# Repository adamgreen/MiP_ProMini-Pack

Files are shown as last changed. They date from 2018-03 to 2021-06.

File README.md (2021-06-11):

# MiP ProMini Pack - 16MHz/5V
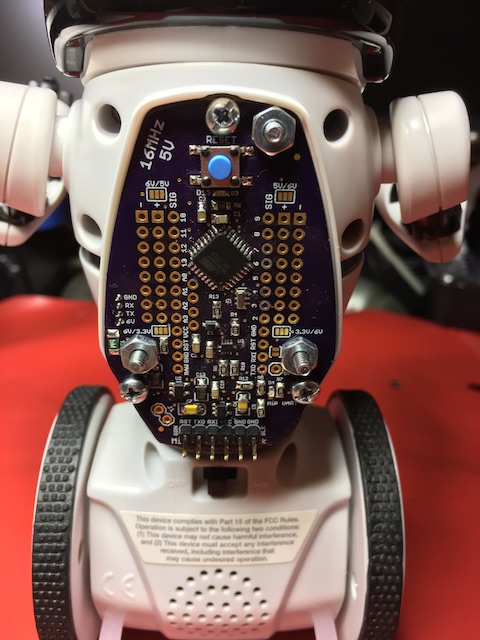
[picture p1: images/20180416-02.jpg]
MiP with ProMini Pack on its back


# Archived - June 10th, 2021
This project is no longer under active development. Both @Tiogaplanet and I have moved onto other projects.

# Attribution
This project is based on the now retired [Sparkfun MiP ProMini-Pack](https://www.sparkfun.com/products/retired/13058).<br>
The original Eagle files can be found on [GitHub](https://github.com/sparkfun/MiP_ProMini-Pack). They were created by
Sparkfun employee [Casey Kuhns](https://github.com/caseykuhns).

# Project Goals
* Produce a functional version of the MiP ProMini-Pack to correct the [MiP communication issue](https://github.com/WowWeeLabs/MiP-BLE-Protocol/issues/18) in the Sparkfun original.
* Run the ATMEGA328 at 16MHz instead of 8MHz. This allows the AVR to properly receive 115200 bps serial output from the
  MiP.
* Increase Vcc from 3.3V to 5V so that the ATMEGA328 can reliably run at 16MHz.
* Modify board layout to make it easier to hand solder the SMD parts.
  * Use larger 0805 passives instead of 0603.
  * Extend the pads on some of the SMD packages to allow for easier transfer of heat from the soldering iron.
* Port my [MiP C API](https://github.com/adamgreen/MiP-Capi) project to Arduino and refactor it to make it more closely resemble other Arduino libraries.
  * This library can be found within the [Arduino/MiP_ProMini_Pack_Library](Arduino/MiP_ProMini_Pack_Library#readme) folder of this GitHub repository.

# Links
* [MiP ProMini-Pack Arduino Library](Arduino/MiP_ProMini_Pack_Library#readme): The Arduino library for this MiP ProMini-Pack.<br>
* [WowWee's Official MiP Protocol Specification](https://github.com/WowWeeLabs/MiP-BLE-Protocol): Describes the serial protocol used by the Arduino library to communicate with the MiP.<br>
* [Sparkfun's MiP ProMini-Pack Installation Tutorial](https://learn.sparkfun.com/tutorials/hacking-the-mip---promini-pack): This retired Sparkfun tutorial is still the best place to learn about opening up your MiP and installing this MiP ProMini Pack.<br>
* [Tiogaplanet's MiP ProtoPack](https://github.com/Tiogaplanet/MiP_ProtoPack): A prototyping plug-in board to expand the MiP ProMini-Pack.<br>

# Bill of Materials
Description | Quantity | Part Number(s)
------------|----------|---------------
[TS3USB221A USB SWITCH DUAL - 10QFN](https://www.digikey.com/products/en?keywords=296-24019-1-ND) | 1 | U3
[ATMEGA328P - 32TQFP](https://www.digikey.com/products/en?keywords=ATMEGA328P-AURCT-ND) | 1 | U1
[16MHz Ceramic Resonator - 15pF ±0.2% SMD](https://www.digikey.com/products/en?keywords=490-1198-1-ND) | 1 | Q1
[MIC5205 Linear Regulator - 5.0V 150mA SOT23-5](https://www.digikey.com/products/en?keywords=576-1261-1-ND) | 1 | U2
[MIC5205 Linear Regulator - 3.3V 150mA SOT23-5](https://www.digikey.com/products/en?keywords=576-1259-1-ND) | 1 | U4
[10kΩ Resistor - 0805](https://www.adafruit.com/product/441) | 3 | R2, R4, R5
[1kΩ Resistor - 0805](https://www.adafruit.com/product/441) | 6 | R7, R8, R9, R10, R12, R13
[330Ω Resistor - 0805](https://www.adafruit.com/product/441) | 1 | R6
[0.1uF Capacitor - 0805](https://www.adafruit.com/product/441) | 6 | C1, C2, C3, C4, C5, C10
[10uF Capacitor - 1206](https://www.digikey.com/products/en?keywords=478-8235-1-ND) | 4 | C6, C7, C13, C19
[Diode Schottky 10V 570mA SOD323](https://www.digikey.com/products/en?keywords=ZLLS410CT-ND) | 1 | D1
[Green LED - 0603](https://www.digikey.com/products/en?keywords=160-1446-1-ND) | 2 | D3, D4
[PTC Resettable Fuse - 1206](https://www.digikey.com/products/en?keywords=507-1802-1-ND) | 1 | F1
[SPST Tactile SMD Switch - Normally Open](https://www.digikey.com/products/en?keywords=CKN9112CT-ND) | 1 | S1
[JST 4-position Connector - 1.5mm Through-Hole](https://www.digikey.com/products/en?keywords=455-1659-ND) | 1 | JP11
[Male Header for FTDI 1x6 - 0.1" Through-Hole](https://www.digikey.com/products/en?keywords=HDR100IMP40M-G-V-TH-ND) | 1 | JP1
[JST 4-wire Cable](https://www.digikey.com/product-detail/en/jst-sales-america-inc/A04ZR04ZR28H152A/455-3026-ND/6009402) | 1 |
[Screw - Phillips Head (1/2", 4-40)](https://www.sparkfun.com/products/10452) | 3 |
[Nut - (4-40)](https://www.sparkfun.com/products/10454) | 3 |
[Screw - Phillip Head (M3-0.5 x 12mm)](https://www.sparkfun.com/products/13227) | 3 |

# Schematic
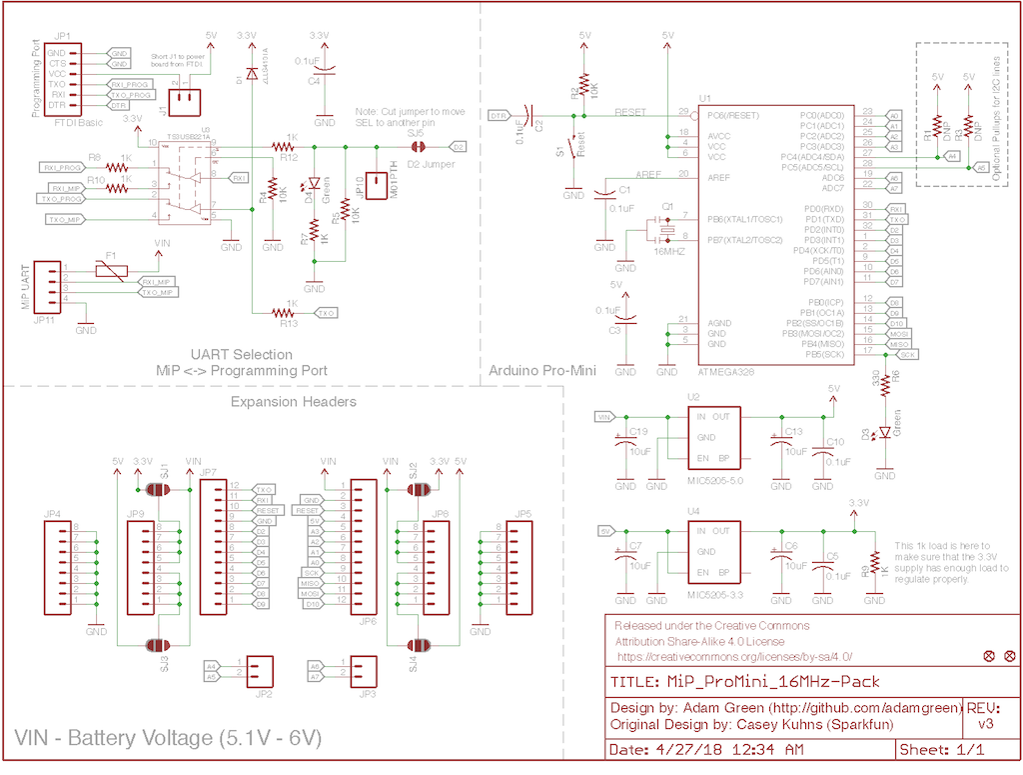
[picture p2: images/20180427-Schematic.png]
Schematic


# OSHPark Renderings of PCB
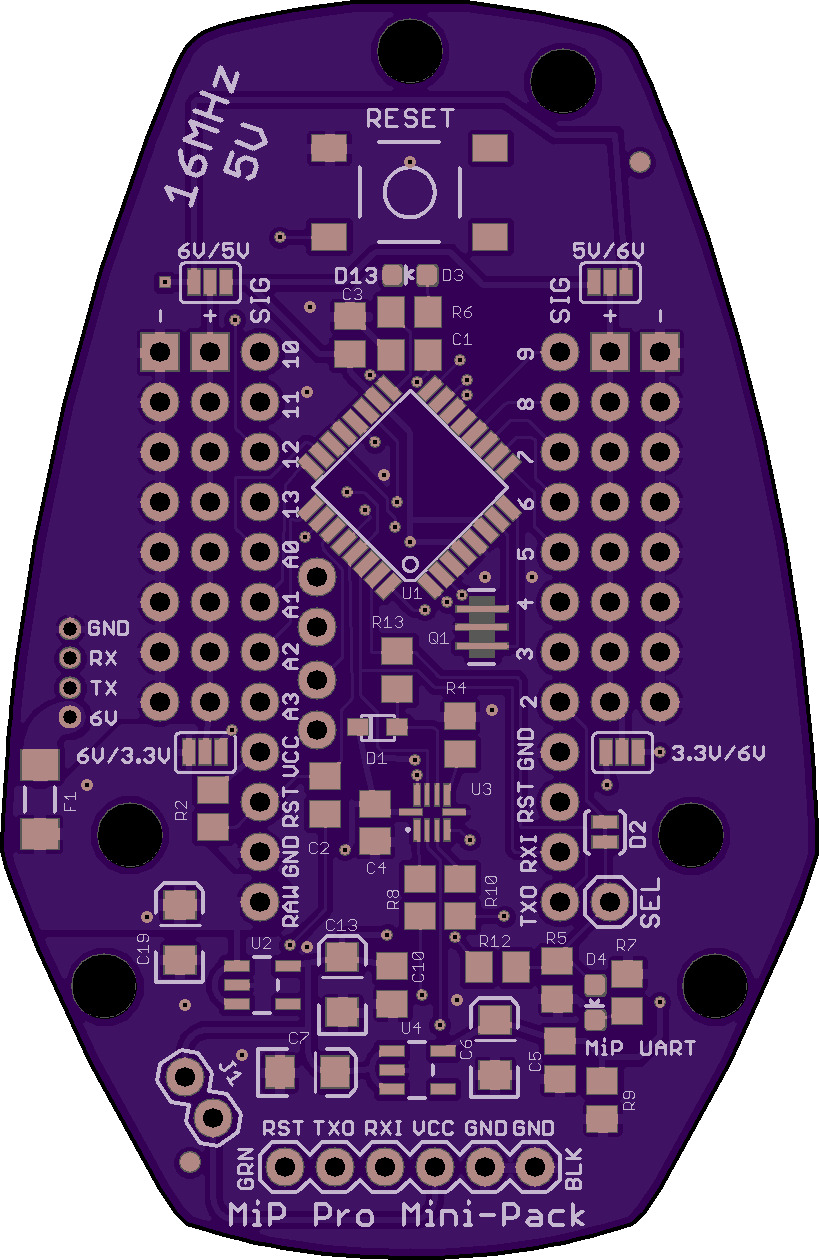
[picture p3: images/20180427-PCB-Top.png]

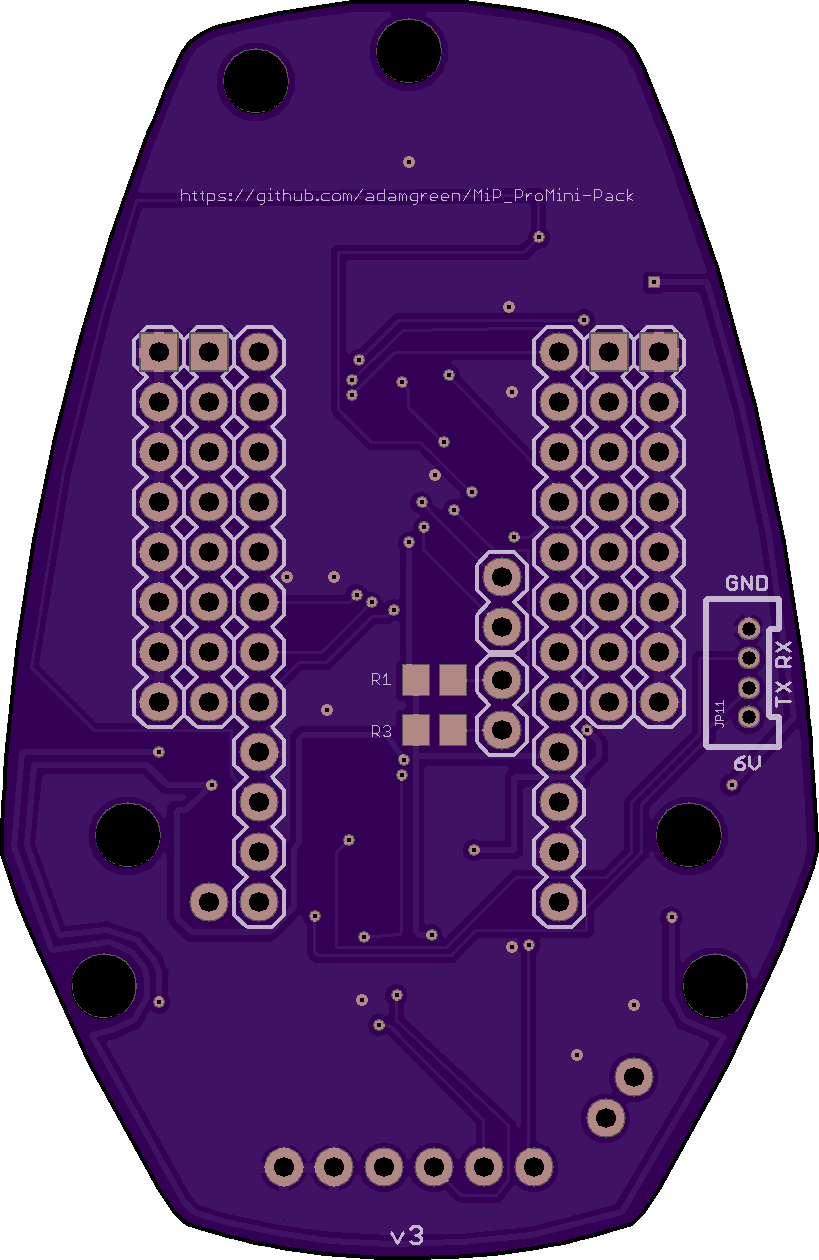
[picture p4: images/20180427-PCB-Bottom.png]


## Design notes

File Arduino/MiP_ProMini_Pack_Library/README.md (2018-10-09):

# MiP ProMini Pack Arduino Library
MiP Photo<br>
The [WowWee MiP](https://wowwee.com/mip) is a hacker friendly self-balancing robot. WowWee not only publish the [MiP Protocol Specification on GitHub](https://github.com/WowWeeLabs/MiP-BLE-Protocol), they also provide a [4-pin hacker port](https://cdn.sparkfun.com/assets/learn_tutorials/2/8/5/HackingPortAnnotated.png), complete with JST connector, right on the mainboard. This connector makes it easy to connect the Arduino compatible [MiP ProMini Pack](https://github.com/adamgreen/MiP_ProMini-Pack) and take control of your MiP. Once connected, you can start:
* Commanding the speed and direction of motion for the gravity defying MiP.
* Commanding the individual control (on, off, blink) of the 4 LED eye segments on the head.
* Taking full control of the RGB LED in the MiP's chest.
* Commanding the playback of sound lists using the >100 built-in sounds.
* Using the head mounted IR sensors to read 'radar' distance measurements or detected user hand gestures.
* Detecting user claps with the built-in microphone.
* Detecting the MiP's current pose via its inertial sensors, the same sensors that make its balancing magic possible.
* And More!

The MiP ProMini Pack was [originally designed by Sparkfun](https://www.sparkfun.com/products/retired/13058) but has since been retired. [This retired Sparkfun tutorial](https://learn.sparkfun.com/tutorials/hacking-the-mip---promini-pack) is still the best place to learn about opening up your MiP and installing the MiP ProMini Pack. Once installed, this is what your MiP will look like:<br>
MiP with ProMini Pack on its back<br>
Once you have it mounted, attach your [FTDI cable](https://www.sparkfun.com/products/9718), [install the MiP ProMini Pack library in the Arduino IDE](https://learn.sparkfun.com/tutorials/installing-an-arduino-library), start hacking and have fun!

## Limitations
One of the cool features that Sparkfun built into the original MiP ProMini Pack is the ability to use the hardware Serial port for communicating with both the MiP and the Arduino IDE's serial monitor. It accomplishes this great feat by using a switch that can direct the Serial traffic to the appropriate target based on the setting of pin 2. Once you call begin() on the MiP object, the Serial traffic will be directed to the MiP except when your code issues print commands such as ```Serial.println("Hello World");```. The library will detect such print calls and automatically direct the resulting Serial traffic to the Arduino IDE and then switch it back to the MiP once the data has been received by the Arduino IDE.

What limitations does this put on your usage of ```Serial.println()``` and ```Serial.print()``` calls?
* Don't use other libraries which send information to the Arduino IDE. Their data will end up being sent to the MiP instead. Only code which ```#include <mip.h>``` will automatically have their print output redirected to the Arduino IDE.
* There are some functions in the library that rely on receiving updates/events that the MiP sends to your Arduino while you are running your awesome code. These include:
  * Radar measurement updates
  * Hand gesture events
  * Battery level updates
  * MiP pose updates (standing upright, laying face down, etc)
  * Clap events
  * Weight updates
  * Shake events
  * Infrared events (detecting other MiPs and receiving their IR codes)
* If you are sending a lot of data to the Arduino IDE in between MiP function calls, you might cause these updates/events to be lost.
* There is a LED labelled **MiP UART** towards the lower right corner of the MiP ProMini Pack. This will be lit when Serial is switched to exchange data with the MiP.
* If you see that it is off most of the time, then you are likely to miss these updates/events.
* If you find your code isn't receiving expected updates/events then double check that you aren't sending too much data to the Arduino IDE.
* It is probably best to not attempt receiving data sent from the Arduino IDE. Calling functions like ```Serial.read()``` from your code is likely to read MiP updates and not Arduino IDE data from the Serial receive buffer.

The original MiP robots communicated over the UART at 115200 baud but the newer ones now communicate at 9600 baud. This library will first start to connect with the MiP at 115200 baud in the MiP::begin() call. If this fails after 5 retries, it will switch to 9600 baud and try again (up to 5 retries). This means that the library should work with both new and old MiP robots but may take a second or so longer to connect to the newer MiP robots when it tries 115200 baud initially.

## Examples
* [ChestLED](https://github.com/adamgreen/MiP_ProMini-Pack/blob/master/Arduino/MiP_ProMini_Pack_Library/examples/ChestLED/ChestLED.ino): Take control of the RGB LED in the chest of the MiP.
* [Clap](https://github.com/adamgreen/MiP_ProMini-Pack/blob/master/Arduino/MiP_ProMini_Pack_Library/examples/Clap/Clap.ino): Send descriptive messages to the Arduino IDE about each clap event deteced by the MiP robot.
* [ContinuousDrive](https://github.com/adamgreen/MiP_ProMini-Pack/blob/master/Arduino/MiP_ProMini_Pack_Library/examples/ContinuousDrive/ContinuousDrive.ino): You want to control the motion of the MiP in real time? This is the example for you.
* [DisconnectApp](https://github.com/adamgreen/MiP_ProMini-Pack/blob/master/Arduino/MiP_ProMini_Pack_Library/examples/DisconnectApp/DisconnectApp.ino): Disconnect all apps, including this sketch and any app that may be connected to Bluetooth.
* [DistanceDrive](https://github.com/adamgreen/MiP_ProMini-Pack/blob/master/Arduino/MiP_ProMini_Pack_Library/examples/DistanceDrive/DistanceDrive.ino): Tell the MiP robot exactly how far to travel and forget about it.
* [DriveForwardBackward](https://github.com/adamgreen/MiP_ProMini-Pack/blob/master/Arduino/MiP_ProMini_Pack_Library/examples/DriveForwardBackward/DriveForwardBackward.ino): Tell the MiP robot how long to drive forward/backward and forget about it.
* [EnableGameMode](https://github.com/adamgreen/MiP_ProMini-Pack/blob/master/Arduino/MiP_ProMini_Pack_Library/examples/EnableGameMode/EnableGameMode.ino): Cycle through each of the game modes available.
* [EnableMiPDetectionMode](https://github.com/adamgreen/MiP_ProMini-Pack/blob/master/Arduino/MiP_ProMini_Pack_Library/examples/EnableMiPDetectionMode/EnableMiPDetectionMode.ino): Allow your MiP to be discovered by others.
* [FallDown](https://github.com/adamgreen/MiP_ProMini-Pack/blob/master/Arduino/MiP_ProMini_Pack_Library/examples/FallDown/FallDown.ino): Tired of standing around? Command MiP to fall flat on his face.
* [Gesture](https://github.com/adamgreen/MiP_ProMini-Pack/blob/master/Arduino/MiP_ProMini_Pack_Library/examples/Gesture/Gesture.ino): Use your hand to make gesture to your MiP robot. Send descriptive messages to the Arduio IDE about each gesture event detected.
* [GestureRadarMode](https://github.com/adamgreen/MiP_ProMini-Pack/blob/master/Arduino/MiP_ProMini_Pack_Library/examples/GestureRadarMode/GestureRadarMode.ino): Want to learn more about how to enable/disable IR based gesture and radar measurements? Check out this example.
* [GetUp](https://github.com/adamgreen/MiP_ProMini-Pack/blob/master/Arduino/MiP_ProMini_Pack_Library/examples/GetUp/GetUp.ino): If your MiP robot falls down, learn how to have him try getting back up on his ~~feet~~wheels.
* [HeadLEDs](https://github.com/adamgreen/MiP_ProMini-Pack/blob/master/Arduino/MiP_ProMini_Pack_Library/examples/HeadLEDs/HeadLEDs.ino): Take control of the 4 individual eye LEDs on the MiP robot's head.
* [Odometer](https://github.com/adamgreen/MiP_ProMini-Pack/blob/master/Arduino/MiP_ProMini_Pack_Library/examples/Odometer/Odometer.ino): How far has your MiP robot been traveling around your personal robot laboratory? This example shows you how to find out and reset its measurement.
* [PlaySound](https://github.com/adamgreen/MiP_ProMini-Pack/blob/master/Arduino/MiP_ProMini_Pack_Library/examples/PlaySound/PlaySound.ino): Learn how to get the MiP robot vocalizing under your control!
* [Radar](https://github.com/adamgreen/MiP_ProMini-Pack/blob/master/Arduino/MiP_ProMini_Pack_Library/examples/Radar/Radar.ino): Is there anything in front of your MiP robot? This example sends descriptive text to the Arduino IDE when it detects changes in the obstacles around it.
* [RawSendReceive](https://github.com/adamgreen/MiP_ProMini-Pack/blob/master/Arduino/MiP_ProMini_Pack_Library/examples/RawSendReceive/RawSendReceive.ino): You found a command in WowWee's Protocol Specification that isn't supported by this library? This example shows you how to experiment with these new commands.
* [ReadWriteEeprom](https://github.com/adamgreen/MiP_ProMini-Pack/blob/master/Arduino/MiP_ProMini_Pack_Library/examples/ReadWriteEeprom/ReadWriteEeprom.ino): Read and write your own data to MiP's EEPROM. This is useful for storing data across power cycles. See also [ZeroEeprom](https://github.com/adamgreen/MiP_ProMini-Pack/blob/master/Arduino/MiP_ProMini_Pack_Library/examples/ZeroEeprom/ZeroEeprom.ino).
* [ReadIRDongleCode](https://github.com/adamgreen/MiP_ProMini-Pack/blob/master/Arduino/MiP_ProMini_Pack_Library/examples/ReadIRDongleCode/ReadIRDongleCode.ino): Reads IR signals sent from another MiP. See also [SendIRDongleCode](https://github.com/adamgreen/MiP_ProMini-Pack/blob/master/Arduino/MiP_ProMini_Pack_Library/examples/SendIRDongleCode/SendIRDongleCode.ino).
* [SendIRDongleCode](https://github.com/adamgreen/MiP_ProMini-Pack/blob/master/Arduino/MiP_ProMini_Pack_Library/examples/SendIRDongleCode/SendIRDongleCode.ino): Sends IR signals to another MiP. See also [ReadIRDongleCode](https://github.com/adamgreen/MiP_ProMini-Pack/blob/master/Arduino/MiP_ProMini_Pack_Library/examples/ReadIRDongleCode/ReadIRDongleCode.ino).
* [SRSdemo](https://github.com/adamgreen/MiP_ProMini-Pack/blob/master/Arduino/MiP_ProMini_Pack_Library/examples/SRSdemo/SRSdemo.ino): The MiP robot made an appearance at the [Seattle Robotics Society](http://www.seattlerobotics.org) meeting on April 21st, 2018. This is what he was running!
* [Shake](https://github.com/adamgreen/MiP_ProMini-Pack/blob/master/Arduino/MiP_ProMini_Pack_Library/examples/Shake/Shake.ino): Is someone shaking your poor little MiP robot? This example shows you how to detect such rudeness and report it to the Arduino IDE.
* [SoftwareHardwareVersion](https://github.com/adamgreen/MiP_ProMini-Pack/blob/master/Arduino/MiP_ProMini_Pack_Library/examples/SoftwareHardwareVersion/SoftwareHardwareVersion.ino): This example shows you how to peek under the covers and see what hardware / software is running inside your MiP robot.
* [Status](https://github.com/adamgreen/MiP_ProMini-Pack/blob/master/Arduino/MiP_ProMini_Pack_Library/examples/Status/Status.ino): Detect changes in the MiP robot's battery level or pose and report them to the Arduino IDE.
* [Stop](https://github.com/adamgreen/MiP_ProMini-Pack/blob/master/Arduino/MiP_ProMini_Pack_Library/examples/Stop/Stop.ino): Danger! Danger! MiP Robot! Stop your MiP robot in its tracks before it gets itself into more trouble.
* [TurnLeftRight](https://github.com/adamgreen/MiP_ProMini-Pack/blob/master/Arduino/MiP_ProMini_Pack_Library/examples/TurnLeftRight/TurnLeftRight.ino): Tell the MiP robot exactly how many degrees to turn and forget about it.
* [Volume](https://github.com/adamgreen/MiP_ProMini-Pack/blob/master/Arduino/MiP_ProMini_Pack_Library/examples/Volume/Volume.ino): Your MiP robot is too loud? Turn down the volume with this example.
* [Weight](https://github.com/adamgreen/MiP_ProMini-Pack/blob/master/Arduino/MiP_ProMini_Pack_Library/examples/Weight/Weight.ino): Detect weight changes in what the MiP is carrying and report them to the Arduino IDE.
* [ZeroEeprom](https://github.com/adamgreen/MiP_ProMini-Pack/blob/master/Arduino/MiP_ProMini_Pack_Library/examples/ZeroEeprom/ZeroEeprom.ino): Write zeroes to each available byte in EEPROM. See also [ReadWriteEeprom](https://github.com/adamgreen/MiP_ProMini-Pack/blob/master/Arduino/MiP_ProMini_Pack_Library/examples/ReadWriteEeprom/ReadWriteEeprom.ino).

## Functions
Group | Function
----- | --------
Initialization  | [MiP()](#mip)
<br>            | [begin()](#begin)
<br>            | [end()](#end)
<br>            | [sleep()](#sleep)
<br>            | [isInitialized()](#isinitialized)
Radar           | [enableRadarMode()](#enableradarmode)
<br>            | [disableRadarMode()](#disableradarmode)
<br>            | [isRadarModeEnabled()](#isradarmodeenabled)
<br>            | [areGestureAndRadarModesDisabled()](#aregestureandradarmodesdisabled)
<br>            | [readRadar()](#readradar)
Gesture         | [enableGestureMode()](#enablegesturemode)
<br>            | [disableGestureMode()](#disablegesturemode)
<br>            | [isGestureModeEnabled()](#isgesturemodeenabled)
<br>            | [areGestureAndRadarModesDisabled()](#aregestureandradarmodesdisabled)
<br>            | [availableGestureEvents()](#availablegestureevents)
<br>            | [readGestureEvent()](#readgestureevent)
Chest LED       | [writeChestLED()](#writechestled)
<br>            | [readChestLED()](#readchestled)
<br>            | [unverifiedWriteChestLED()](#unverifiedwritechestled)
Head LEDs       | [writeHeadLEDs()](#writeheadleds)
<br>            | [readHeadLEDs()](#readheadleds)
<br>            | [unverifiedWriteHeadLEDs()](#unverifiedwriteheadleds)
Motion          | [continuousDrive()](#continuousdrive)
<br>            | [distanceDrive()](#distancedrive)
<br>            | [turnLeft()](#turnleft)
<br>            | [turnRight()](#turnright)
<br>            | [driveForward()](#driveforward)
<br>            | [driveBackward()](#drivebackward)
<br>            | [stop()](#stop)
<br>            | [fallForward()](#fallforward)
<br>            | [fallBackward()](#fallbackward)
<br>            | [getUp()](#getup)
Sound           | [playSound()](#playsound)
<br>            | [beginSoundList()](#beginsoundlist)
<br>            | [addEntryToSoundList()](#addentrytosoundlist)
<br>            | [playSoundList()](#playsoundlist)
<br>            | [writeVolume()](#writevolume)
<br>            | [readVolume()](#readvolume)
Odometer        | [readDistanceTravelled()](#readdistancetravelled)
<br>            | [resetDistanceTravelled()](#resetdistancetravelled)
Battery Level   | [readBatteryVoltage()](#readbatteryvoltage)
Position        | [readPosition()](#readposition)
<br>            | [isOnBack()](#isonback)
<br>            | [isFaceDown()](#isfacedown)
<br>            | [isUpright()](#isupright)
<br>            | [isPickedUp()](#ispickedup)
<br>            | [isHandStanding()](#ishandstanding)
<br>            | [isFaceDownOnTray()](#isfacedownontray)
<br>            | [isOnBackWithKickstand()](#isonbackwithkickstand)
Weight          | [readWeight()](#readweight)
Clap            | [enableClapEvents()](#enableclapevents)
<br>            | [disableClapEvents()](#disableclapevents)
<br>            | [areClapEventsEnabled()](#areclapeventsenabled)
<br>            | [writeClapDelay()](#writeclapdelay)
<br>            | [readClapDelay()](#readclapdelay)
<br>            | [availableClapEvents()](#availableclapevents)
<br>            | [readClapEvent()](#readclapevent)
Shake           | [hasBeenShaken()](#hasbeenshaken)
Version Info    | [readSoftwareVersion()](#readsoftwareversion)
<br>            | [readHardwareInfo()](#readhardwareinfo)
Game Modes      | [enableAppMode()](#enableappmode)
<br>            | [enableCageMode()](#enablecagemode)
<br>            | [enableDanceMode()](#enabledancemode)
<br>            | [enableStackMode()](#enablestackmode)
<br>            | [enableTrickMode()](#enabletrickmode)
<br>            | [enableRoamMode()](#enableroammode)
<br>            | [isAppModeEnabled()](#isappmodeenabled)
<br>            | [isCageModeEnabled()](#iscagemodeenabled)
<br>            | [isDanceModeEnabled()](#isdancemodeenabled)
<br>            | [isStackModeEnabled()](#isstackmodeenabled)
<br>            | [isTrickModeEnabled()](#istrickmodeenabled)
<br>            | [isRoamModeEnabled()](#isroammodeenabled)
EEPROM          | [setUserData()](#setUserData)
<br>            | [getUserData()](#getUserData)
Infrared        | [enableMiPDetectionMode()](#enablemipdetectionmode)
<br>            | [disableMiPDetectionMode()](#disablemipdetectionmode)
<br>            | [isMiPDetectionModeEnabled()](#ismipdetectionmodeenabled)
<br>            | [readDetectedMiP()](#readdetectedmip)
<br>            | [availableDetectedMiPEvents()](#availabledetectedmipevents)
<br>            | [sendIRDongleCode()](#sendirdonglecode)
<br>            | [readIRDongleCode()](#readirdonglecode)
<br>            | [availableIRCodeEvents()](#availableircodeevents)

---
### MiP()
```MiP(int8_t serialSelectPin = MIP_UART_SELECT_PIN)```
#### Description
This MiP constructor is used to create an instance of a MiP object, whose name you need to provide as in the example below. Only one MiP object should be created in your sketch.

You still need to call [begin()](#begin) to initialize communication with the MiP before calling any other MiP functions.

#### Parameters
* **serialSelectPin** is the pin used to switch the Serial output between the MiP and Arduino IDE. It defaults to MIP_UART_SELECT_PIN, pin 2. The MiP ProMini Pack hardware is designed to use this pin as well. Switching serialSelectPin to another pin would therefore require that you make hardware changes to the MiP ProMini Pack as well.

#### Returns
Nothing

#### Example
```c++
// Include the MiP library so that you can use its functions.
#include <mip.h>

// Setup new MiP object.
MiP     mip;
```

---
### begin()
```bool MiP::begin()```
#### Description
Initializes the MiP robot to be controlled by the Arduino instead of Bluetooth Low Energy. The LED on the chest of the MiP robot will switch from blue to green once this switch has been made. The MiP robot requires a power reset to switch out of serial mode and accept Bluetooth Low Energy connections again.

Calling another MiP function before begin() has successfully been called will typically generate an error message and your program will be halted so that you can diagnose and correct the problem.

[isInitialized()](#isinitialized) can be called to determine if begin() has been successfully called or not.

#### Parameters
None

#### Returns
* **true** if the MiP robot was successfully initialized.
* **false** if begin() failed to properly initialize the MiP robot.

#### Example
```c++
// Include the MiP library so that you can use its functions.
#include <mip.h>

// Setup new MiP object.
MiP     mip;

void setup() {
  // Call begin() to initialize the MiP robot.
  // Returns false if it fails to initialize the MiP robot.
  bool connectResult = mip.begin();
  if (!connectResult) {
    Serial.println(F("Failed connecting to MiP!"));
    return;
  }

  // ...
}

void loop() {
  // ...
}
```

---
### end()
```void end()```
#### Description
Disconnects from the MiP, disables serial communication, and allows the Serial Rx/Tx pins and serialSelectPin to be used for general input/output.

[isInitialized()](#isinitialized) will return false after end() has been called.

#### Parameters
None

#### Returns
Nothing

#### Example
```c++
  mip.end();
```

---
### sleep()
```void sleep()```
#### Description
Puts the MiP to sleep. The MiP robot will need to be shut off and back on to wake it from this sleep. Calling [begin()](#begin) will not wake it.

#### Parameters
None

#### Returns
Nothing

#### Example
```c++
#include <mip.h>

MiP     mip;

void setup() {
  bool connectResult = mip.begin();
  if (!connectResult) {
    Serial.println(F("Failed connecting to MiP!"));
    return;
  }

  Serial.println(F("Sleep.ino - Shows begin()/end()/sleep() functionality."));
  Serial.println(F("Chest LED should be green to indicate UART connection."));

  delay(5000);
  Serial.println(F("Disconnecting from MiP. Chest LED should revert to blue."));
  mip.end();

  delay(5000);
  Serial.println(F("Attempting to reconnect to MiP. Chest LED should turn green again."));
  connectResult = mip.begin();
  if (!connectResult) {
    Serial.println(F("Failed reconnecting to MiP!"));
    return;
  }

  delay(5000);
  Serial.println(F("Putting MiP to sleep. Will require power cycle before it will accept UART connections again."));
  mip.sleep();
}

void loop() {
}
```

---
### isInitialized()
```bool isInitialized()```
#### Description
Returns whether [begin()](#begin) has been called successfully yet or not.

#### Parameters
None

#### Returns
* **true** if the MiP robot was successfully initialized.<br>
* **false** if begin() failed to properly initialize the MiP robot or [end()](#end) has been called since the successful begin().

#### Example
```c++
  if (!mip.isInitialized()) {
    // Handle the fact that the MiP robot hasn't been initialized yet.
  }
```

---
### enableRadarMode()
```void enableRadarMode()```
#### Description
Switches the MiP robot's head mounted IR sensors into radar mode. Once this mode is enabled, your code can call [readRadar()](#readradar) to read the radar measurements.

#### Parameters
None

#### Returns
Nothing

#### Notes
* When enableRadarMode() is called, gesture mode will be disabled. If you later enable gesture mode, radar mode will be disabled.

#### Example
```c++
#include <mip.h>

MiP     mip;

void setup() {
  bool connectResult = mip.begin();
  if (!connectResult) {
    Serial.println(F("Failed connecting to MiP!"));
    return;
  }

  Serial.println(F("Radar.ino - Display current radar readings to user."));

  Serial.println(F("Waiting for robot to be standing upright."));
  while (!mip.isUpright()) {
    // Waiting
  }
  mip.enableRadarMode();
}

void loop() {
  static MiPRadar lastRadar = MIP_RADAR_INVALID;
  MiPRadar        currentRadar = mip.readRadar();

  if (currentRadar != MIP_RADAR_INVALID && lastRadar != currentRadar) {
    Serial.print(F("Radar = "));
    switch (currentRadar) {
      case MIP_RADAR_NONE:
        Serial.println(F("None"));
        break;
      case MIP_RADAR_10CM_30CM:
        Serial.println(F("10cm - 30cm"));
        break;
      case MIP_RADAR_0CM_10CM:
        Serial.println(F("0cm - 10cm"));
        break;
      default:
        break;
    }
    lastRadar = currentRadar;
  }
}
```

---
### disableRadarMode()
```void disableRadarMode()```
#### Description
Switches the MiP robot's head mounted IR sensors out of radar mode.

#### Parameters
None

#### Returns
Nothing

#### Notes
* Calling disableRadarMode() actually disables all IR sensing so it will also shutdown gesture mode as well.

#### Example
```c++
#include <mip.h>

MiP     mip;

void setup() {
  bool connectResult = mip.begin();
  if (!connectResult) {
    Serial.println(F("Failed connecting to MiP!"));
    return;
  }

  Serial.println(F("GestureRadarMode.ino - Switches between gesture, radar, and default modes."));

  Serial.println(F("Calling mip.enableRadarMode()"));
  mip.enableRadarMode();
  Serial.print(F("mip.isRadarModeEnabled() = "));
  if (mip.isRadarModeEnabled()) {
    Serial.println(F("true - Pass"));
  } else {
    Serial.println(F("false - Failed"));
  }

  Serial.println(F("Calling mip.disableRadarMode()"));
  mip.disableRadarMode();
  Serial.print(F("mip.isRadarModeEnabled() = "));
  if (mip.isRadarModeEnabled()) {
    Serial.println(F("true - Failed"));
  } else {
    Serial.println(F("false - Pass"));
  }

  Serial.println(F("Calling mip.enableGestureMode()"));
  mip.enableGestureMode();
  Serial.print(F("mip.isGestureModeEnabled() = "));
  if (mip.isGestureModeEnabled()) {
    Serial.println(F("true - Pass"));
  } else {
    Serial.println(F("false - Failed"));
  }

  Serial.println(F("Calling mip.disableGestureMode()"));
  mip.disableGestureMode();
  Serial.print(F("mip.isGestureModeEnabled() = "));
  if (mip.isGestureModeEnabled()) {
    Serial.println(F("true - Failed"));
  } else {
    Serial.println(F("false - Pass"));
  }
  Serial.print(F("mip.areGestureAndRadarModesDisabled() = "));
  if (mip.areGestureAndRadarModesDisabled()) {
    Serial.println(F("true - Pass"));
  } else {
    Serial.println(F("false - Failed"));
  }

  Serial.println();
  Serial.println(F("Sample done."));
}

void loop() {
}
```

---
### isRadarModeEnabled()
```bool isRadarModeEnabled()```
#### Description
Returns whether the MiP robot's head mounted IR sensors are in radar mode.

#### Parameters
None

#### Returns
* **true** if the MiP robot was successfully placed in radar mode with a previous call to [enableRadarMode()](#enableradarmode).
* **false** if it is not in radar mode.

#### Example
```c++
#include <mip.h>

MiP     mip;

void setup() {
  bool connectResult = mip.begin();
  if (!connectResult) {
    Serial.println(F("Failed connecting to MiP!"));
    return;
  }

  Serial.println(F("GestureRadarMode.ino - Switches between gesture, radar, and default modes."));

  Serial.println(F("Calling mip.enableRadarMode()"));
  mip.enableRadarMode();
  Serial.print(F("mip.isRadarModeEnabled() = "));
  if (mip.isRadarModeEnabled()) {
    Serial.println(F("true - Pass"));
  } else {
    Serial.println(F("false - Failed"));
  }

  Serial.println(F("Calling mip.disableRadarMode()"));
  mip.disableRadarMode();
  Serial.print(F("mip.isRadarModeEnabled() = "));
  if (mip.isRadarModeEnabled()) {
    Serial.println(F("true - Failed"));
  } else {
    Serial.println(F("false - Pass"));
  }

  Serial.println(F("Calling mip.enableGestureMode()"));
  mip.enableGestureMode();
  Serial.print(F("mip.isGestureModeEnabled() = "));
  if (mip.isGestureModeEnabled()) {
    Serial.println(F("true - Pass"));
  } else {
    Serial.println(F("false - Failed"));
  }

  Serial.println(F("Calling mip.disableGestureMode()"));
  mip.disableGestureMode();
  Serial.print(F("mip.isGestureModeEnabled() = "));
  if (mip.isGestureModeEnabled()) {
    Serial.println(F("true - Failed"));
  } else {
    Serial.println(F("false - Pass"));
  }
  Serial.print(F("mip.areGestureAndRadarModesDisabled() = "));
  if (mip.areGestureAndRadarModesDisabled()) {
    Serial.println(F("true - Pass"));
  } else {
    Serial.println(F("false - Failed"));
  }

  Serial.println();
  Serial.println(F("Sample done."));
}

void loop() {
}
```

---
### areGestureAndRadarModesDisabled()
```bool areGestureAndRadarModesDisabled()```
#### Description
Returns whether the MiP robot's head mounted IR sensors are inactive, not performing radar measurements or gesture detection.

#### Parameters
None

#### Returns
* **true** if the MiP robot is not in gesture detection or radar measurement mode.
* **false** if it is in gesture detection or radar measurement mode.

#### Example
```c++
#include <mip.h>

MiP     mip;

void setup() {
  bool connectResult = mip.begin();
  if (!connectResult) {
    Serial.println(F("Failed connecting to MiP!"));
    return;
  }

  Serial.println(F("GestureRadarMode.ino - Switches between gesture, radar, and default modes."));

  Serial.println(F("Calling mip.enableRadarMode()"));
  mip.enableRadarMode();
  Serial.print(F("mip.isRadarModeEnabled() = "));
  if (mip.isRadarModeEnabled()) {
    Serial.println(F("true - Pass"));
  } else {
    Serial.println(F("false - Failed"));
  }

  Serial.println(F("Calling mip.disableRadarMode()"));
  mip.disableRadarMode();
  Serial.print(F("mip.isRadarModeEnabled() = "));
  if (mip.isRadarModeEnabled()) {
    Serial.println(F("true - Failed"));
  } else {
    Serial.println(F("false - Pass"));
  }

  Serial.println(F("Calling mip.enableGestureMode()"));
  mip.enableGestureMode();
  Serial.print(F("mip.isGestureModeEnabled() = "));
  if (mip.isGestureModeEnabled()) {
    Serial.println(F("true - Pass"));
  } else {
    Serial.println(F("false - Failed"));
  }

  Serial.println(F("Calling mip.disableGestureMode()"));
  mip.disableGestureMode();
  Serial.print(F("mip.isGestureModeEnabled() = "));
  if (mip.isGestureModeEnabled()) {
    Serial.println(F("true - Failed"));
  } else {
    Serial.println(F("false - Pass"));
  }
  Serial.print(F("mip.areGestureAndRadarModesDisabled() = "));
  if (mip.areGestureAndRadarModesDisabled()) {
    Serial.println(F("true - Pass"));
  } else {
    Serial.println(F("false - Failed"));
  }

  Serial.println();
  Serial.println(F("Sample done."));
}

void loop() {
}
```

---
### readRadar()
```MiPRadar readRadar()```
#### Description
Reads the current radar measurement from the MiP robot's head mounted IR sensors. The MiP robot must have already been placed in radar mode via a call to [enableRadarMode()](#enableradarmode).

#### Parameters
None

#### Returns
* **MIP_RADAR_NONE** if no object has been detected in front of the MiP's head.
* **MIP_RADAR_10CM_30CM** if an object has been detected between 10cm and 30cm in front of the MiP's head.
* **MIP_RADAR_0CM_10CM** if an object has been detected at less than 10cm in front of the MiP's head.
* **MIP_RADAR_INVALID** if the MiP robot hasn't sent back a radar measurement. This could happen for a few reasons:
  * You just called enableRadarMode() and the MiP robot hasn't had a chance to make its first reading yet.
  * The MiP robot isn't currently in radar mode. Call enableRadarMode() to let it know that it should start taking these measurements.
  * You are spending so much time sending output back to the serial monitor in the Arduino IDE that the MiP's radar measurements are getting dropped. See [Limitations](#limitations) section above.

#### Notes
* These radar measurements will be suppressed while the MiP is executing long running commands. Shorter commands like mipContinuousDrive() do allow the MiP to make the measurements.
* These radar measurements will only be sent when the MiP is actively balancing. They will be suppressed if the MiP is laying back on its kickstand for example.

#### Example
```c++
#include <mip.h>

MiP     mip;

void setup() {
  bool connectResult = mip.begin();
  if (!connectResult) {
    Serial.println(F("Failed connecting to MiP!"));
    return;
  }

  Serial.println(F("Radar.ino - Display current radar readings to user."));

  Serial.println(F("Waiting for robot to be standing upright."));
  while (!mip.isUpright()) {
    // Waiting
  }
  mip.enableRadarMode();
}

void loop() {
  static MiPRadar lastRadar = MIP_RADAR_INVALID;
  MiPRadar        currentRadar = mip.readRadar();

  if (currentRadar != MIP_RADAR_INVALID && lastRadar != currentRadar) {
    Serial.print(F("Radar = "));
    switch (currentRadar) {
      case MIP_RADAR_NONE:
        Serial.println(F("None"));
        break;
      case MIP_RADAR_10CM_30CM:
        Serial.println(F("10cm - 30cm"));
        break;
      case MIP_RADAR_0CM_10CM:
        Serial.println(F("0cm - 10cm"));
        break;
      default:
        break;
    }
    lastRadar = currentRadar;
  }
}
```

---
### enableGestureMode()
```void enableGestureMode()```
#### Description
Switches the MiP robot's head mounted IR sensors into gesture detection mode. Once this mode is enabled, you can call [availableGestureEvents()](#availablegestureevents) and [readGestureEvent()](#readgestureevent) to read gesture events as the MiP detects them.

#### Parameters
None

#### Returns
Nothing

#### Notes
* When enableGestureMode() is called, radar mode will be disabled. If you later enable radar mode, gesture mode will be disabled.

#### Example
```c++
#include <mip.h>

MiP     mip;

void setup() {
  bool connectResult = mip.begin();
  if (!connectResult) {
    Serial.println(F("Failed connecting to MiP!"));
    return;
  }

  Serial.println(F("Gesture.ino - Detect gesture and inform user as they occur."));

  Serial.println(F("Waiting for robot to be standing upright."));
  while (!mip.isUpright()) {
    // Waiting
  }
  mip.enableGestureMode();
}

void loop() {
  while (mip.availableGestureEvents() > 0) {
    MiPGesture gesture = mip.readGestureEvent();
    Serial.print(F("Detected "));
    switch (gesture) {
      case MIP_GESTURE_LEFT:
        Serial.println(F("Left gesture!"));
        break;
      case MIP_GESTURE_RIGHT:
        Serial.println(F("Right gesture!"));
        break;
      case MIP_GESTURE_CENTER_SWEEP_LEFT:
        Serial.println(F("Center Sweep Left gesture!"));
        break;
      case MIP_GESTURE_CENTER_SWEEP_RIGHT:
        Serial.println(F("Center Sweep Right gesture!"));
        break;
      case MIP_GESTURE_CENTER_HOLD:
        Serial.println(F("Center Hold gesture!"));
        break;
      case MIP_GESTURE_FORWARD:
        Serial.println(F("Forward gesture!"));
        break;
      case MIP_GESTURE_BACKWARD:
        Serial.println(F("Backward gesture!"));
        break;
      case MIP_GESTURE_INVALID:
        // This shouldn't really happen since mip.availableGestureEvents() returned > 0.
        Serial.println(F("INVALID gesture!"));
        break;
    }
  }
}
```

---
### disableGestureMode()
```void disableGestureMode()```
#### Description
Switches the MiP robot's head mounted IR sensors out of gesture detection mode.

#### Parameters
None

#### Returns
Nothing

#### Notes
* Calling disableGestureMode() actually disables all IR sensing so it will also shutdown radar mode as well.

#### Example
```c++
#include <mip.h>

MiP     mip;

void setup() {
  bool connectResult = mip.begin();
  if (!connectResult) {
    Serial.println(F("Failed connecting to MiP!"));
    return;
  }

  Serial.println(F("GestureRadarMode.ino - Switches between gesture, radar, and default modes."));

  Serial.println(F("Calling mip.enableRadarMode()"));
  mip.enableRadarMode();
  Serial.print(F("mip.isRadarModeEnabled() = "));
  if (mip.isRadarModeEnabled()) {
    Serial.println(F("true - Pass"));
  } else {
    Serial.println(F("false - Failed"));
  }

  Serial.println(F("Calling mip.disableRadarMode()"));
  mip.disableRadarMode();
  Serial.print(F("mip.isRadarModeEnabled() = "));
  if (mip.isRadarModeEnabled()) {
    Serial.println(F("true - Failed"));
  } else {
    Serial.println(F("false - Pass"));
  }

  Serial.println(F("Calling mip.enableGestureMode()"));
  mip.enableGestureMode();
  Serial.print(F("mip.isGestureModeEnabled() = "));
  if (mip.isGestureModeEnabled()) {
    Serial.println(F("true - Pass"));
  } else {
    Serial.println(F("false - Failed"));
  }

  Serial.println(F("Calling mip.disableGestureMode()"));
  mip.disableGestureMode();
  Serial.print(F("mip.isGestureModeEnabled() = "));
  if (mip.isGestureModeEnabled()) {
    Serial.println(F("true - Failed"));
  } else {
    Serial.println(F("false - Pass"));
  }
  Serial.print(F("mip.areGestureAndRadarModesDisabled() = "));
  if (mip.areGestureAndRadarModesDisabled()) {
    Serial.println(F("true - Pass"));
  } else {
    Serial.println(F("false - Failed"));
  }

  Serial.println();
  Serial.println(F("Sample done."));
}

void loop() {
}
```

---
### isGestureModeEnabled()
```bool isGestureModeEnabled()```
#### Description
Returns whether the MiP robot's head mounted IR sensors are in gesture detection mode.

#### Parameters
None

#### Returns
* **true** if the MiP robot was successfully placed in gesture detection mode with a previous call to [enableGestureMode()](#enablegesturemode).
* **false** if it is not in gesture detection mode.

#### Example
```c++
#include <mip.h>

MiP     mip;

void setup() {
  bool connectResult = mip.begin();
  if (!connectResult) {
    Serial.println(F("Failed connecting to MiP!"));
    return;
  }

  Serial.println(F("GestureRadarMode.ino - Switches between gesture, radar, and default modes."));

  Serial.println(F("Calling mip.enableRadarMode()"));
  mip.enableRadarMode();
  Serial.print(F("mip.isRadarModeEnabled() = "));
  if (mip.isRadarModeEnabled()) {
    Serial.println(F("true - Pass"));
  } else {
    Serial.println(F("false - Failed"));
  }

  Serial.println(F("Calling mip.disableRadarMode()"));
  mip.disableRadarMode();
  Serial.print(F("mip.isRadarModeEnabled() = "));
  if (mip.isRadarModeEnabled()) {
    Serial.println(F("true - Failed"));
  } else {
    Serial.println(F("false - Pass"));
  }

  Serial.println(F("Calling mip.enableGestureMode()"));
  mip.enableGestureMode();
  Serial.print(F("mip.isGestureModeEnabled() = "));
  if (mip.isGestureModeEnabled()) {
    Serial.println(F("true - Pass"));
  } else {
    Serial.println(F("false - Failed"));
  }

  Serial.println(F("Calling mip.disableGestureMode()"));
  mip.disableGestureMode();
  Serial.print(F("mip.isGestureModeEnabled() = "));
  if (mip.isGestureModeEnabled()) {
    Serial.println(F("true - Failed"));
  } else {
    Serial.println(F("false - Pass"));
  }
  Serial.print(F("mip.areGestureAndRadarModesDisabled() = "));
  if (mip.areGestureAndRadarModesDisabled()) {
    Serial.println(F("true - Pass"));
  } else {
    Serial.println(F("false - Failed"));
  }

  Serial.println();
  Serial.println(F("Sample done."));
}

void loop() {
}
```

---
### availableGestureEvents()
```uint8_t availableGestureEvents()```
#### Description
Returns the number of gesture detection events that the library currently has sitting in its queue, ready to be read by calling [readGestureEvent()](#readgestureevent). The MiP robot must have already been placed in gesture detection mode via a call to [enableGestureMode()](#enablegesturemode) for new gesture detection events to be added to this queue.

#### Parameters
None

#### Returns
* **0** if there are currently no gesture detection events ready for reading. Calling [readGestureEvent()](#readgestureevent) now would retun MIP_GESTURE_INVALID.
* **Non-zero** value indicates the number of readGestureEvent() calls that can be made and successfully return a valid gesture detection event.

#### Notes
* These gesture detection events will be suppressed while the MiP is executing long running commands. Shorter commands like mipContinuousDrive() do allow the MiP to make the gesture detections.
* These gesture detection events will only be sent when the MiP is actively balancing. They will be suppressed if the MiP is laying back on its kickstand for example.
* The maximum number of gesture detection events that can be queued up between calls to readGestureEvent() is 8. If this count is exceeded, the oldest events will be overwritten.

#### Example
```c++
#include <mip.h>

MiP     mip;

void setup() {
  bool connectResult = mip.begin();
  if (!connectResult) {
    Serial.println(F("Failed connecting to MiP!"));
    return;
  }

  Serial.println(F("Gesture.ino - Detect gesture and inform user as they occur."));

  Serial.println(F("Waiting for robot to be standing upright."));
  while (!mip.isUpright()) {
    // Waiting
  }
  mip.enableGestureMode();
}

void loop() {
  while (mip.availableGestureEvents() > 0) {
    MiPGesture gesture = mip.readGestureEvent();
    Serial.print(F("Detected "));
    switch (gesture) {
      case MIP_GESTURE_LEFT:
        Serial.println(F("Left gesture!"));
        break;
      case MIP_GESTURE_RIGHT:
        Serial.println(F("Right gesture!"));
        break;
      case MIP_GESTURE_CENTER_SWEEP_LEFT:
        Serial.println(F("Center Sweep Left gesture!"));
        break;
      case MIP_GESTURE_CENTER_SWEEP_RIGHT:
        Serial.println(F("Center Sweep Right gesture!"));
        break;
      case MIP_GESTURE_CENTER_HOLD:
        Serial.println(F("Center Hold gesture!"));
        break;
      case MIP_GESTURE_FORWARD:
        Serial.println(F("Forward gesture!"));
        break;
      case MIP_GESTURE_BACKWARD:
        Serial.println(F("Backward gesture!"));
        break;
      case MIP_GESTURE_INVALID:
        // This shouldn't really happen since mip.availableGestureEvents() returned > 0.
        Serial.println(F("INVALID gesture!"));
        break;
    }
  }
}
```

---
### readGestureEvent()
```MiPGesture readGestureEvent()```
#### Description
Returns a gesture detection event from the library's queue. They will be returned in the order that the MiP robot detected them. The MiP robot must have already been placed in gesture detection mode via a call to [enableGestureMode()](#enablegesturemode) for new gesture detection events to be added to this queue.

#### Parameters
None

#### Returns
* **MIP_GESTURE_INVALID** if the gesture detection event queue is empty. [availableGestureEvents()](#availablegestureevents) would return 0 in this scenario.

| Other Valid Return Values       |
| ------------------------------- |
| MIP_GESTURE_LEFT                |
| MIP_GESTURE_RIGHT               |
| MIP_GESTURE_CENTER_SWEEP_LEFT   |
| MIP_GESTURE_CENTER_SWEEP_RIGHT  |
| MIP_GESTURE_CENTER_HOLD         |
| MIP_GESTURE_FORWARD             |
| MIP_GESTURE_BACKWARD            |

#### Notes
* These gesture detection events will be suppressed while the MiP is executing long running commands. Shorter commands like mipContinuousDrive() do allow the MiP to make the gesture detections.
* These gesture detection events will only be sent when the MiP is actively balancing. They will be suppressed if the MiP is laying back on its kickstand for example.
* The maximum number of gesture detection events that can be queued up between calls to readGestureEvent() is 8. If this count is exceeded, the oldest events will be overwritten.

#### Example
```c++
#include <mip.h>

MiP     mip;

void setup() {
  bool connectResult = mip.begin();
  if (!connectResult) {
    Serial.println(F("Failed connecting to MiP!"));
    return;
  }

  Serial.println(F("Gesture.ino - Detect gesture and inform user as they occur."));

  Serial.println(F("Waiting for robot to be standing upright."));
  while (!mip.isUpright()) {
    // Waiting
  }
  mip.enableGestureMode();
}

void loop() {
  while (mip.availableGestureEvents() > 0) {
    MiPGesture gesture = mip.readGestureEvent();
    Serial.print(F("Detected "));
    switch (gesture) {
      case MIP_GESTURE_LEFT:
        Serial.println(F("Left gesture!"));
        break;
      case MIP_GESTURE_RIGHT:
        Serial.println(F("Right gesture!"));
        break;
      case MIP_GESTURE_CENTER_SWEEP_LEFT:
        Serial.println(F("Center Sweep Left gesture!"));
        break;
      case MIP_GESTURE_CENTER_SWEEP_RIGHT:
        Serial.println(F("Center Sweep Right gesture!"));
        break;
      case MIP_GESTURE_CENTER_HOLD:
        Serial.println(F("Center Hold gesture!"));
        break;
      case MIP_GESTURE_FORWARD:
        Serial.println(F("Forward gesture!"));
        break;
      case MIP_GESTURE_BACKWARD:
        Serial.println(F("Backward gesture!"));
        break;
      case MIP_GESTURE_INVALID:
        // This shouldn't really happen since mip.availableGestureEvents() returned > 0.
        Serial.println(F("INVALID gesture!"));
        break;
    }
  }
}
```

---
### writeChestLED()
```void writeChestLED(uint8_t red, uint8_t green, uint8_t blue)```<br>
```void writeChestLED(uint8_t red, uint8_t green, uint8_t blue, uint16_t onTime, uint16_t offTime)```<br>
```void writeChestLED(const MiPChestLED& chestLED)```
#### Description
Sets the colour and flashing period of the RGB LED in the MiP robot's chest.

#### Parameters
* **red** is the intensity of the red colour channel (0 - 255).
* **green** is the intensity of the green colour channel (0 - 255).
* **blue** is the intensity of the blue colour channel (0 - 255). The MiP robot actually clears the lower 2 bits of the blue colour channel to treat it as a 6-bit value.
* **onTime** is the time in milliseconds that the LED should remain on with the specified colour. This parameter can be set to a value between 0 and 5100 milliseconds.
* **offTime** is the time in milliseconds that the LED should remain off before turning on again with the specified colour. This parameter can be set to a value between 0 and 5100 milliseconds.
* **chestLED** is an object which contains red, green, blue, onTime, and offTime fields for setting the LED colour and flashing period.
```c++
class MiPChestLED
{
    // ...
    uint16_t onTime;
    uint16_t offTime;
    uint8_t  red;
    uint8_t  green;
    uint8_t  blue;
};
```

#### Returns
Nothing

#### Notes
* The MiP only supports a granularity of 20 milliseconds for the onTime and offTime parameters.
* The ```void writeChestLED(uint8_t red, uint8_t green, uint8_t blue)``` version can only set the LED to a solid colour with no flashing.

#### Example
```c++
#include <mip.h>

MiP     mip;

void setup() {
  bool connectResult = mip.begin();
  if (!connectResult) {
    Serial.println(F("Failed connecting to MiP!"));
    return;
  }

  Serial.println(F("ChestLED.ino - Set Chest LED to different colors.\n"));

  Serial.println(F("Set chest LED to magenta."));
  uint8_t red = 0xff;
  uint8_t green = 0x01;
  uint8_t blue = 0xfe;
  mip.writeChestLED(red, green, blue);
  printCurrentChestLEDSetting();
  delay(1000);

  Serial.println(F("Set chest LED to blink red."));
  red = 0xff;
  green = 0x01;
  blue = 0x05;
  const uint16_t onTime = 990;
  const uint16_t offTime = 989;
  mip.writeChestLED(red, green, blue, onTime, offTime);
  printCurrentChestLEDSetting();
  delay(4000);

  Serial.println(F("Set chest LED back to green."));
  MiPChestLED chestLED;
  chestLED.red = 0x00;
  chestLED.green = 0xff;
  chestLED.blue = 0x00;
  chestLED.onTime = 0;
  chestLED.offTime = 0;
  mip.writeChestLED(chestLED);
  printCurrentChestLEDSetting();
  delay(1000);

  // Attempt to run through the same sequence of chest LED changes using the
  // unverifiedWriteChestLED() functions which don't always get accepted by the MiP.
  Serial.println(F("Trying to set chest LED to magenta."));
  red = 0xff;
  green = 0x01;
  blue = 0xfe;
  mip.unverifiedWriteChestLED(red, green, blue);
  delay(1000);

  Serial.println(F("Trying to set chest LED to blink red."));
  red = 0xff;
  green = 0x01;
  blue = 0x05;
  mip.unverifiedWriteChestLED(red, green, blue, onTime, offTime);
  delay(4000);

  Serial.println(F("Trying to set chest LED back to green."));
  chestLED.red = 0x00;
  chestLED.green = 0xff;
  chestLED.blue = 0x00;
  chestLED.onTime = 0;
  chestLED.offTime = 0;
  mip.unverifiedWriteChestLED(chestLED);
  delay(1000);

  Serial.println();
  Serial.println(F("Sample done."));
}

void loop() {
}

static void printCurrentChestLEDSetting() {
  MiPChestLED chestLED;
  mip.readChestLED(chestLED);

  Serial.println(F("Current Chest LED Setting"));
  Serial.print(F("    red: "));
    Serial.println(chestLED.red);
  Serial.print(F("    green: "));
    Serial.println(chestLED.green);
  Serial.print(F("    blue: "));
    Serial.println(chestLED.blue);
  Serial.print(F("    on time: "));
    Serial.print(chestLED.onTime);
    Serial.println(F(" milliseconds"));
  Serial.print(F("    off time: "));
    Serial.print(chestLED.offTime);
    Serial.println(F(" milliseconds"));
  Serial.println();
}
```

---
### readChestLED()
```void readChestLED(MiPChestLED& chestLED)```
#### Description
Reads the current setting for the colour and flashing period of the RGB LED in the MiP robot's chest.

#### Parameters
* **chestLED** is an object which contains red, green, blue, onTime, and offTime fields to be filled in with the current LED colour and flashing period.
```c++
class MiPChestLED
{
    // ...
    uint16_t onTime;
    uint16_t offTime;
    uint8_t  red;
    uint8_t  green;
    uint8_t  blue;
};
```

#### Returns
Nothing

#### Example
```c++
#include <mip.h>

MiP     mip;

void setup() {
  bool connectResult = mip.begin();
  if (!connectResult) {
    Serial.println(F("Failed connecting to MiP!"));
    return;
  }

  Serial.println(F("ChestLED.ino - Set Chest LED to different colors.\n"));

  Serial.println(F("Set chest LED to magenta."));
  uint8_t red = 0xff;
  uint8_t green = 0x01;
  uint8_t blue = 0xfe;
  mip.writeChestLED(red, green, blue);
  printCurrentChestLEDSetting();
  delay(1000);

  Serial.println(F("Set chest LED to blink red."));
  red = 0xff;
  green = 0x01;
  blue = 0x05;
  const uint16_t onTime = 990;
  const uint16_t offTime = 989;
  mip.writeChestLED(red, green, blue, onTime, offTime);
  printCurrentChestLEDSetting();
  delay(4000);

  Serial.println(F("Set chest LED back to green."));
  MiPChestLED chestLED;
  chestLED.red = 0x00;
  chestLED.green = 0xff;
  chestLED.blue = 0x00;
  chestLED.onTime = 0;
  chestLED.offTime = 0;
  mip.writeChestLED(chestLED);
  printCurrentChestLEDSetting();
  delay(1000);

  // Attempt to run through the same sequence of chest LED changes using the
  // unverifiedWriteChestLED() functions which don't always get accepted by the MiP.
  Serial.println(F("Trying to set chest LED to magenta."));
  red = 0xff;
  green = 0x01;
  blue = 0xfe;
  mip.unverifiedWriteChestLED(red, green, blue);
  delay(1000);

  Serial.println(F("Trying to set chest LED to blink red."));
  red = 0xff;
  green = 0x01;
  blue = 0x05;
  mip.unverifiedWriteChestLED(red, green, blue, onTime, offTime);
  delay(4000);

  Serial.println(F("Trying to set chest LED back to green."));
  chestLED.red = 0x00;
  chestLED.green = 0xff;
  chestLED.blue = 0x00;
  chestLED.onTime = 0;
  chestLED.offTime = 0;
  mip.unverifiedWriteChestLED(chestLED);
  delay(1000);

  Serial.println();
  Serial.println(F("Sample done."));
}

void loop() {
}

static void printCurrentChestLEDSetting() {
  MiPChestLED chestLED;
  mip.readChestLED(chestLED);

  Serial.println(F("Current Chest LED Setting"));
  Serial.print(F("    red: "));
    Serial.println(chestLED.red);
  Serial.print(F("    green: "));
    Serial.println(chestLED.green);
  Serial.print(F("    blue: "));
    Serial.println(chestLED.blue);
  Serial.print(F("    on time: "));
    Serial.print(chestLED.onTime);
    Serial.println(F(" milliseconds"));
  Serial.print(F("    off time: "));
    Serial.print(chestLED.offTime);
    Serial.println(F(" milliseconds"));
  Serial.println();
}
```

---
### unverifiedWriteChestLED()
```void unverifiedWriteChestLED(uint8_t red, uint8_t green, uint8_t blue)```<br>
```void unverifiedWriteChestLED(uint8_t red, uint8_t green, uint8_t blue, uint16_t onTime, uint16_t offTime)```<br>
```void unverifiedWriteChestLED(const MiPChestLED& chestLED)```
#### Description
Sets the colour and flashing period of the RGB LED in the MiP robot's chest. These functions operate similarily to the [writeChestLED()](#writechestled) functions except that these ones are faster since they don't bother to verify that the MiP actually sets the LED state as requested. Typically you would want to use the writeChestLED() functions but these unverified ones can be useful when you are calling them several times per second so that a missed LED state update won't be noticed by the user.

#### Parameters
* **red** is the intensity of the red colour channel (0 - 255).
* **green** is the intensity of the green colour channel (0 - 255).
* **blue** is the intensity of the blue colour channel (0 - 255). The MiP robot actually clears the lower 2 bits of the blue colour channel to treat it as a 6-bit value.
* **onTime** is the time in milliseconds that the LED should remain on with the specified colour. This parameter can be set to a value between 0 and 5100 milliseconds.
* **offTime** is the time in milliseconds that the LED should remain off before turning on again with the specified colour. This parameter can be set to a value between 0 and 5100 milliseconds.
* **chestLED** is an object which contains red, green, blue, onTime, and offTime fields for setting the LED colour and flashing period.
```c++
class MiPChestLED
{
    // ...
    uint16_t onTime;
    uint16_t offTime;
    uint8_t  red;
    uint8_t  green;
    uint8_t  blue;
};
```

#### Returns
Nothing

#### Notes
* The MiP only supports a granularity of 20 milliseconds for the onTime and offTime parameters.
* The ```void writeChestLED(uint8_t red, uint8_t green, uint8_t blue)``` version can only set the LED to a solid colour with no flashing.

#### Example
```c++
#include <mip.h>

MiP     mip;

void setup() {
  bool connectResult = mip.begin();
  if (!connectResult) {
    Serial.println(F("Failed connecting to MiP!"));
    return;
  }

  Serial.println(F("ChestLED.ino - Set Chest LED to different colors.\n"));

  Serial.println(F("Set chest LED to magenta."));
  uint8_t red = 0xff;
  uint8_t green = 0x01;
  uint8_t blue = 0xfe;
  mip.writeChestLED(red, green, blue);
  printCurrentChestLEDSetting();
  delay(1000);

  Serial.println(F("Set chest LED to blink red."));
  red = 0xff;
  green = 0x01;
  blue = 0x05;
  const uint16_t onTime = 990;
  const uint16_t offTime = 989;
  mip.writeChestLED(red, green, blue, onTime, offTime);
  printCurrentChestLEDSetting();
  delay(4000);

  Serial.println(F("Set chest LED back to green."));
  MiPChestLED chestLED;
  chestLED.red = 0x00;
  chestLED.green = 0xff;
  chestLED.blue = 0x00;
  chestLED.onTime = 0;
  chestLED.offTime = 0;
  mip.writeChestLED(chestLED);
  printCurrentChestLEDSetting();
  delay(1000);

  // Attempt to run through the same sequence of chest LED changes using the
  // unverifiedWriteChestLED() functions which don't always get accepted by the MiP.
  Serial.println(F("Trying to set chest LED to magenta."));
  red = 0xff;
  green = 0x01;
  blue = 0xfe;
  mip.unverifiedWriteChestLED(red, green, blue);
  delay(1000);

  Serial.println(F("Trying to set chest LED to blink red."));
  red = 0xff;
  green = 0x01;
  blue = 0x05;
  mip.unverifiedWriteChestLED(red, green, blue, onTime, offTime);
  delay(4000);

  Serial.println(F("Trying to set chest LED back to green."));
  chestLED.red = 0x00;
  chestLED.green = 0xff;
  chestLED.blue = 0x00;
  chestLED.onTime = 0;
  chestLED.offTime = 0;
  mip.unverifiedWriteChestLED(chestLED);
  delay(1000);

  Serial.println();
  Serial.println(F("Sample done."));
}

void loop() {
}

static void printCurrentChestLEDSetting() {
  MiPChestLED chestLED;
  mip.readChestLED(chestLED);

  Serial.println(F("Current Chest LED Setting"));
  Serial.print(F("    red: "));
    Serial.println(chestLED.red);
  Serial.print(F("    green: "));
    Serial.println(chestLED.green);
  Serial.print(F("    blue: "));
    Serial.println(chestLED.blue);
  Serial.print(F("    on time: "));
    Serial.print(chestLED.onTime);
    Serial.println(F(" milliseconds"));
  Serial.print(F("    off time: "));
    Serial.print(chestLED.offTime);
    Serial.println(F(" milliseconds"));
  Serial.println();
}
```

---
### writeHeadLEDs()
```void writeHeadLEDs(MiPHeadLED led1, MiPHeadLED led2, MiPHeadLED led3, MiPHeadLED led4)```<br>
```void writeHeadLEDs(const MiPHeadLEDs& headLEDs)```<br>
#### Description
Sets the state of the four eye LEDs on the MiP robot's head.

#### Parameters
* **led1** sets the state of led1 on the MiP robot's head. Valid states are **MIP_HEAD_LED_OFF**, **MIP_HEAD_LED_ON**, **MIP_HEAD_LED_BLINK_SLOW**, **MIP_HEAD_LED_BLINK_FAST**.
* **led2** sets the state of led2 on the MiP robot's head. Valid states are **MIP_HEAD_LED_OFF**, **MIP_HEAD_LED_ON**, **MIP_HEAD_LED_BLINK_SLOW**, **MIP_HEAD_LED_BLINK_FAST**.
* **led3** sets the state of led3 on the MiP robot's head. Valid states are **MIP_HEAD_LED_OFF**, **MIP_HEAD_LED_ON**, **MIP_HEAD_LED_BLINK_SLOW**, **MIP_HEAD_LED_BLINK_FAST**.
* **led4** sets the state of led4 on the MiP robot's head. Valid states are **MIP_HEAD_LED_OFF**, **MIP_HEAD_LED_ON**, **MIP_HEAD_LED_BLINK_SLOW**, **MIP_HEAD_LED_BLINK_FAST**.
* **headLEDs** is an object which contains led1, led2, led3, and led4 fields for setting the state of all 4 LEDs.
```c++
class MiPHeadLEDs
{
public:
    // ...
    MiPHeadLED led1;
    MiPHeadLED led2;
    MiPHeadLED led3;
    MiPHeadLED led4;
};
```

#### Returns
Nothing

#### Notes
* The 4 head LEDs are numbered from left to right, with led1 being the leftmost and led4 being the rightmost.

#### Example
```c++
#include <mip.h>

MiP     mip;

void setup() {
  bool connectResult = mip.begin();
  if (!connectResult) {
    Serial.println(F("Failed connecting to MiP!"));
    return;
  }

  Serial.println(F("HeadLEDs.ino - Use head LED functions. Should set each head LED to different state."));
  mip.writeHeadLEDs(MIP_HEAD_LED_OFF, MIP_HEAD_LED_ON, MIP_HEAD_LED_BLINK_SLOW, MIP_HEAD_LED_BLINK_FAST);

  MiPHeadLEDs headLEDs;
  mip.readHeadLEDs(headLEDs);
  Serial.println(F("Head LEDs"));
  Serial.print(F("    led1: "));
    printLEDString(headLEDs.led1);
  Serial.print(F("    led2: "));
    printLEDString(headLEDs.led2);
  Serial.print(F("    led3: "));
    printLEDString(headLEDs.led3);
  Serial.print(F("    led4: "));
    printLEDString(headLEDs.led4);

  delay(4000);

  // Turn all the LEDs back on now.
  Serial.println(F("Turning all eye LEDs back on now."));
  headLEDs.led1 = headLEDs.led2 = headLEDs.led3 = headLEDs.led4 = MIP_HEAD_LED_ON;
  mip.writeHeadLEDs(headLEDs);
  delay(1000);

  // Attempt to run through the same sequence of head LED changes using the
  // unverifiedWriteHeadLEDs() functions which don't always get accepted by the MiP.
  Serial.println(F("Trying to set each head LED to a different state."));
  mip.unverifiedWriteHeadLEDs(MIP_HEAD_LED_OFF, MIP_HEAD_LED_ON, MIP_HEAD_LED_BLINK_SLOW, MIP_HEAD_LED_BLINK_FAST);
  delay(4000);

  Serial.println(F("Trying to set all eye LEDs back on now."));
  headLEDs.led1 = headLEDs.led2 = headLEDs.led3 = headLEDs.led4 = MIP_HEAD_LED_ON;
  mip.unverifiedWriteHeadLEDs(headLEDs);

  Serial.println();
  Serial.println(F("Sample done."));
}

static void printLEDString(MiPHeadLED led) {
  switch (led) {
    case MIP_HEAD_LED_OFF:
      Serial.println(F("Off"));
      break;
    case MIP_HEAD_LED_ON:
      Serial.println(F("On"));
      break;
    case MIP_HEAD_LED_BLINK_SLOW:
      Serial.println(F("Blink Slow"));
      break;
    case MIP_HEAD_LED_BLINK_FAST:
      Serial.println(F("Blink Fast"));
      break;
    default:
      Serial.println();
      break;
  }
}

void loop() {
}
```

---
### readHeadLEDs()
```void readHeadLEDs(MiPHeadLEDs& headLEDs)```
#### Description
Reads the current setting for the MiP robot's four head LEDs.

#### Parameters
* **headLEDs** is an object which contains led1, led2, led3, and led4 fields to be filled in with the current state of all 4 LEDs.
```c++
class MiPHeadLEDs
{
public:
    // ...
    MiPHeadLED led1;
    MiPHeadLED led2;
    MiPHeadLED led3;
    MiPHeadLED led4;
};
```

#### Returns
Nothing

#### Notes
* The 4 head LEDs are numbered from left to right, with led1 being the leftmost and led4 being the rightmost.

#### Example
```c++
#include <mip.h>

MiP     mip;

void setup() {
  bool connectResult = mip.begin();
  if (!connectResult) {
    Serial.println(F("Failed connecting to MiP!"));
    return;
  }

  Serial.println(F("HeadLEDs.ino - Use head LED functions. Should set each head LED to different state."));
  mip.writeHeadLEDs(MIP_HEAD_LED_OFF, MIP_HEAD_LED_ON, MIP_HEAD_LED_BLINK_SLOW, MIP_HEAD_LED_BLINK_FAST);

  MiPHeadLEDs headLEDs;
  mip.readHeadLEDs(headLEDs);
  Serial.println(F("Head LEDs"));
  Serial.print(F("    led1: "));
    printLEDString(headLEDs.led1);
  Serial.print(F("    led2: "));
    printLEDString(headLEDs.led2);
  Serial.print(F("    led3: "));
    printLEDString(headLEDs.led3);
  Serial.print(F("    led4: "));
    printLEDString(headLEDs.led4);

  delay(4000);

  // Turn all the LEDs back on now.
  Serial.println(F("Turning all eye LEDs back on now."));
  headLEDs.led1 = headLEDs.led2 = headLEDs.led3 = headLEDs.led4 = MIP_HEAD_LED_ON;
  mip.writeHeadLEDs(headLEDs);
  delay(1000);

  // Attempt to run through the same sequence of head LED changes using the
  // unverifiedWriteHeadLEDs() functions which don't always get accepted by the MiP.
  Serial.println(F("Trying to set each head LED to a different state."));
  mip.unverifiedWriteHeadLEDs(MIP_HEAD_LED_OFF, MIP_HEAD_LED_ON, MIP_HEAD_LED_BLINK_SLOW, MIP_HEAD_LED_BLINK_FAST);
  delay(4000);

  Serial.println(F("Trying to set all eye LEDs back on now."));
  headLEDs.led1 = headLEDs.led2 = headLEDs.led3 = headLEDs.led4 = MIP_HEAD_LED_ON;
  mip.unverifiedWriteHeadLEDs(headLEDs);

  Serial.println();
  Serial.println(F("Sample done."));
}

static void printLEDString(MiPHeadLED led) {
  switch (led) {
    case MIP_HEAD_LED_OFF:
      Serial.println(F("Off"));
      break;
    case MIP_HEAD_LED_ON:
      Serial.println(F("On"));
      break;
    case MIP_HEAD_LED_BLINK_SLOW:
      Serial.println(F("Blink Slow"));
      break;
    case MIP_HEAD_LED_BLINK_FAST:
      Serial.println(F("Blink Fast"));
      break;
    default:
      Serial.println();
      break;
  }
}

void loop() {
}
```

---
### unverifiedWriteHeadLEDs()
```void unverifiedWriteHeadLEDs(MiPHeadLED led1, MiPHeadLED led2, MiPHeadLED led3, MiPHeadLED led4)```<br>
```void unverifiedWriteHeadLEDs(const MiPHeadLEDs& headLEDs)```<br>
#### Description
Sets the state of the four eye LEDs on the MiP robot's head. These functions operate similarily to the [writeHeadLEDs()](#writeheadleds) functions except that these ones are faster since they don't bother to verify that the MiP actually sets the LED state as requested. Typically you would want to use the writeHeadLEDs() functions but these unverified ones can be useful when you are calling them several times per second so that a missed LED state update won't be noticed by the user.

#### Parameters
* **led1** sets the state of led1 on the MiP robot's head. Valid states are **MIP_HEAD_LED_OFF**, **MIP_HEAD_LED_ON**, **MIP_HEAD_LED_BLINK_SLOW**, **MIP_HEAD_LED_BLINK_FAST**.
* **led2** sets the state of led2 on the MiP robot's head. Valid states are **MIP_HEAD_LED_OFF**, **MIP_HEAD_LED_ON**, **MIP_HEAD_LED_BLINK_SLOW**, **MIP_HEAD_LED_BLINK_FAST**.
* **led3** sets the state of led3 on the MiP robot's head. Valid states are **MIP_HEAD_LED_OFF**, **MIP_HEAD_LED_ON**, **MIP_HEAD_LED_BLINK_SLOW**, **MIP_HEAD_LED_BLINK_FAST**.
* **led4** sets the state of led4 on the MiP robot's head. Valid states are **MIP_HEAD_LED_OFF**, **MIP_HEAD_LED_ON**, **MIP_HEAD_LED_BLINK_SLOW**, **MIP_HEAD_LED_BLINK_FAST**.
* **headLEDs** is an object which contains led1, led2, led3, and led4 fields for setting the state of all 4 LEDs.
```c++
class MiPHeadLEDs
{
public:
    // ...
    MiPHeadLED led1;
    MiPHeadLED led2;
    MiPHeadLED led3;
    MiPHeadLED led4;
};
```

#### Returns
Nothing

#### Notes
* The 4 head LEDs are numbered from left to right, with led1 being the leftmost and led4 being the rightmost.

#### Example
```c++
#include <mip.h>

MiP     mip;

void setup() {
  bool connectResult = mip.begin();
  if (!connectResult) {
    Serial.println(F("Failed connecting to MiP!"));
    return;
  }

  Serial.println(F("HeadLEDs.ino - Use head LED functions. Should set each head LED to different state."));
  mip.writeHeadLEDs(MIP_HEAD_LED_OFF, MIP_HEAD_LED_ON, MIP_HEAD_LED_BLINK_SLOW, MIP_HEAD_LED_BLINK_FAST);

  MiPHeadLEDs headLEDs;
  mip.readHeadLEDs(headLEDs);
  Serial.println(F("Head LEDs"));
  Serial.print(F("    led1: "));
    printLEDString(headLEDs.led1);
  Serial.print(F("    led2: "));
    printLEDString(headLEDs.led2);
  Serial.print(F("    led3: "));
    printLEDString(headLEDs.led3);
  Serial.print(F("    led4: "));
    printLEDString(headLEDs.led4);

  delay(4000);

  // Turn all the LEDs back on now.
  Serial.println(F("Turning all eye LEDs back on now."));
  headLEDs.led1 = headLEDs.led2 = headLEDs.led3 = headLEDs.led4 = MIP_HEAD_LED_ON;
  mip.writeHeadLEDs(headLEDs);
  delay(1000);

  // Attempt to run through the same sequence of head LED changes using the
  // unverifiedWriteHeadLEDs() functions which don't always get accepted by the MiP.
  Serial.println(F("Trying to set each head LED to a different state."));
  mip.unverifiedWriteHeadLEDs(MIP_HEAD_LED_OFF, MIP_HEAD_LED_ON, MIP_HEAD_LED_BLINK_SLOW, MIP_HEAD_LED_BLINK_FAST);
  delay(4000);

  Serial.println(F("Trying to set all eye LEDs back on now."));
  headLEDs.led1 = headLEDs.led2 = headLEDs.led3 = headLEDs.led4 = MIP_HEAD_LED_ON;
  mip.unverifiedWriteHeadLEDs(headLEDs);

  Serial.println();
  Serial.println(F("Sample done."));
}

static void printLEDString(MiPHeadLED led) {
  switch (led) {
    case MIP_HEAD_LED_OFF:
      Serial.println(F("Off"));
      break;
    case MIP_HEAD_LED_ON:
      Serial.println(F("On"));
      break;
    case MIP_HEAD_LED_BLINK_SLOW:
      Serial.println(F("Blink Slow"));
      break;
    case MIP_HEAD_LED_BLINK_FAST:
      Serial.println(F("Blink Fast"));
      break;
    default:
      Serial.println();
      break;
  }
}

void loop() {
}
```

---
### continuousDrive()
```void continuousDrive(int8_t velocity, int8_t turnRate)```
#### Description
Instruct the MiP robot to drive in a particular direction.

#### Parameters
* **velocity** is the forward/reverse velocity.  This parameter can have a value between -32 and 32, where -32 is maximum  reverse velocity and 32 is maximum forward velocity.  A velocity of 0 indicates that no forward/reverse motion is desired at this time.
* **turnRate** is the amount of left/right turn rate.  This parameter can have a value between -32 and 32, where -32 is  maximum left turn rate and 32 is maximum right turn velocity.  A turn rate of 0 indicates that no left/right turning is desired at this time.

#### Returns
Nothing

#### Notes
* This command must be sent at regular intervals to keep the MiP robot moving in the desired direction.  This interval  should be ~50 milliseconds. If you send them faster than this interval, they will be ignored by the library so as not to overload the MiP robot.
* When sent at longer intervals the MiP robot's motion will become more jerky as it thinks that there will not be another  motion command coming so it starts to stop all motion and then starts moving again once the next command does finally arrive.
* If your robot code is constantly sensing it's environment and using those ongoing sensor readings to make decisions on which direction the robot should be currently headed, then this command will be the most useful for updating the MiP's motion in real time.
* Radar measurements and gesture detection events will still be generated by the MiP robot when continuous drive commands are being sent to it.

#### Example
```c++
#include <mip.h>

MiP     mip;

void setup() {
  bool connectResult = mip.begin();
  if (!connectResult) {
    Serial.println(F("Failed connecting to MiP!"));
    return;
  }

  Serial.println(F("ContinuousDrive.ino - Use continuousDrive() function. Drive forward with right turn and then backward with left turn."));
}

void loop()
{
  static enum States {
    RIGHT_TURN,
    LEFT_TURN,
    DONE
  } state = RIGHT_TURN;
  static uint32_t startTime = millis();
  uint32_t        currentTime = millis();
  uint32_t        elapsedTime = currentTime - startTime;

  switch (state) {
    case RIGHT_TURN:
      if (elapsedTime < 2000) {
        // Drive forward at half-speed and turn right at quarter rate.
        mip.continuousDrive(16, 8);
      } else {
        startTime = currentTime;
        state = LEFT_TURN;
      }
      break;
    case LEFT_TURN:
      if (elapsedTime < 2000) {
        // Drive backward at half-speed and turn left at quarter rate.
        mip.continuousDrive(-16, -8);
      } else {
        Serial.println();
        Serial.println(F("Sample done."));
        state = DONE;
      }
      break;
    default:
      break;
  }
}
```

---
### distanceDrive()
```void distanceDrive(MiPDriveDirection driveDirection, uint8_t cm, MiPTurnDirection turnDirection, uint16_t degrees)```
#### Description
Used to queue up a drive/turn command to the MiP robot.

#### Parameters
* **driveDirection** specifies the direction the robot should drive: **MIP_DRIVE_FORWARD** or **MIP_DRIVE_BACKWARD**.
* **cm** specifies the number of centimeters the robot should proceed in driveDirection.  This parameter can have a value between 0 and 255 cm.  Can be set to 0 if only a turn is desired.
* **turnDirection** specifies the direction the robot should turn: **MIP_TURN_LEFT** or **MIP_TURN_RIGHT**.
* **degrees** is the number of degrees the robot should turn.  This parameter can have a value between 0 and 360 degrees.  Can be set to 0 if only a forward/reverse drive is desired.

#### Returns
Nothing

#### Notes
* It is possible to queue up to 20 of these distance drive commands in the MiP's memory.
* There is no way to specify the speed to be used for driving and/or turning.
* The distance travelled isn't super accurate.  Usually it travels further than commanded.

#### Example
```c++
#include <mip.h>

MiP     mip;

void setup() {
  bool connectResult = mip.begin();
  if (!connectResult) {
    Serial.println(F("Failed connecting to MiP!"));
    return;
  }

  Serial.println(F("DistanceDrive.ino - Use distanceDrive function. Drive forward, turn 360 degrees in each direction and backward."));

  // Queue up multiple commands to run in sequence.
  mip.distanceDrive(MIP_DRIVE_FORWARD, 30, MIP_TURN_RIGHT, 0);
  mip.distanceDrive(MIP_DRIVE_FORWARD, 0, MIP_TURN_LEFT, 360);
  mip.distanceDrive(MIP_DRIVE_FORWARD, 0, MIP_TURN_RIGHT, 360);
  mip.distanceDrive(MIP_DRIVE_BACKWARD, 30, MIP_TURN_RIGHT, 0);

  Serial.println();
  Serial.println(F("Sample done."));
}

void loop() {
}
```

---
### turnLeft()
```void turnLeft(uint16_t degrees, uint8_t speed)```
#### Description
Commands the MiP robot to turn left the desired number of degrees at the desired speed.

#### Parameters
* **degrees** specifies the number of degrees the robot should turn.  This parameter can have a value between 0 and 1275 degrees.
* **speed** is the speed at which the turn should take place.  The speed can have a value between 0 and 24 with 0 being the slowest rate and 24 the fastest.

#### Returns
Nothing

#### Example
```c++
#include <mip.h>

MiP     mip;

void setup() {
  bool connectResult = mip.begin();
  if (!connectResult) {
    Serial.println(F("Failed connecting to MiP!"));
    return;
  }

  Serial.println(F("TurnLeftRight.ino - Use turnLeft & turnRight() functions. Turn 180 degrees to left and then 180 degrees to right."));

  mip.turnLeft(180, 12);
  delay(2000);
  mip.turnRight(180, 12);
  delay(2000);

  Serial.println();
  Serial.println(F("Sample done."));
}

void loop() {
}
```

---
### turnRight()
```void turnRight(uint16_t degrees, uint8_t speed)```
#### Description
Commands the MiP robot to turn right the desired number of degrees at the desired speed.

#### Parameters
* **degrees** specifies the number of degrees the robot should turn.  This parameter can have a value between 0 and 1275 degrees.
* **speed** is the speed at which the turn should take place.  The speed can have a value between 0 and 24 with 0 being the slowest rate and 24 the fastest.

#### Returns
Nothing

#### Example
```c++
#include <mip.h>

MiP     mip;

void setup() {
  bool connectResult = mip.begin();
  if (!connectResult) {
    Serial.println(F("Failed connecting to MiP!"));
    return;
  }

  Serial.println(F("TurnLeftRight.ino - Use turnLeft & turnRight() functions. Turn 180 degrees to left and then 180 degrees to right."));

  mip.turnLeft(180, 12);
  delay(2000);
  mip.turnRight(180, 12);
  delay(2000);

  Serial.println();
  Serial.println(F("Sample done."));
}

void loop() {
}
```

---
### driveForward()
```void driveForward(uint8_t speed, uint16_t time)```
#### Description
Commands the MiP robot to drive forward.

#### Parameters
* **speed** specifies the speed at which the motion should take place.  The speed can have a value between 0 and 30 with 0 being the slowest rate and 30 the fastest.
* **time** specifies the time to drive forward in milliseconds.  This parameter can have a value between 0 and 1785 milliseconds. The MiP only supports a granularity of 7 milliseconds for this parameter.

#### Returns
Nothing

#### Example
```c++
#include <mip.h>

MiP     mip;

void setup() {
  bool connectResult = mip.begin();
  if (!connectResult) {
    Serial.println(F("Failed connecting to MiP!"));
    return;
  }

  Serial.println(F("DriveForwardBackward.ino - Use driveForward() & driveBackward() functions. Drive ahead and back, 1 second in each direction."));

  mip.driveForward(15, 1000);
  delay(2000);
  mip.driveBackward(15, 1000);
  delay(2000);

  Serial.println();
  Serial.println(F("Sample done."));
}

void loop() {
}
```

---
### driveBackward()
```void driveBackward(uint8_t speed, uint16_t time)```
#### Description
Commands the MiP robot to drive backward.

#### Parameters
* **speed** specifies the speed at which the motion should take place.  The speed can have a value between 0 and 30 with 0 being the slowest rate and 30 the fastest.
* **time** specifies the time to drive backward in milliseconds.  This parameter can have a value between 0 and 1785 milliseconds. The MiP only supports a granularity of 7 milliseconds for this parameter.

#### Returns
Nothing

#### Example
```c++
#include <mip.h>

MiP     mip;

void setup() {
  bool connectResult = mip.begin();
  if (!connectResult) {
    Serial.println(F("Failed connecting to MiP!"));
    return;
  }

  Serial.println(F("DriveForwardBackward.ino - Use driveForward() & driveBackward() functions. Drive ahead and back, 1 second in each direction."));

  mip.driveForward(15, 1000);
  delay(2000);
  mip.driveBackward(15, 1000);
  delay(2000);

  Serial.println();
  Serial.println(F("Sample done."));
}

void loop() {
}
```

---
### stop()
```void stop()```
#### Description
Interrupt and stop current MiP robot motion.

#### Parameters
None

#### Returns
Nothing

#### Example
```c++
#include <mip.h>

MiP     mip;

void setup() {
  bool connectResult = mip.begin();
  if (!connectResult) {
    Serial.println(F("Failed connecting to MiP!"));
    return;
  }

  Serial.println(F("Stop.ino - Use stop() function. Interrupt a 360 degree turn with stop()."));

  mip.turnLeft(360, 6);
  delay(1000);
  mip.stop();
  delay(1000);

  Serial.println();
  Serial.println(F("Sample done."));
}

void loop() {
}
```

---
### fallForward()
```void fallForward()```
#### Description
Have the MiP fall forward.

#### Parameters
None

#### Returns
Nothing

#### Example
```c++
#include <mip.h>

MiP     mip;

void setup() {
  bool connectResult = mip.begin();
  if (!connectResult) {
    Serial.println(F("Failed connecting to MiP!"));
    return;
  }

  Serial.println(F("FallDown.ino - Fall forward and backward.\n"));

  Serial.println(F("Waiting for robot to be standing upright."));
  while (!mip.isUpright()) {
    // Waiting
  }
  delay(1000);

  Serial.println(F("Falling forward."));
  mip.fallForward();

  delay(1000);
  Serial.println(F("Waiting for robot to be standing upright again."));
  while (!mip.isUpright()) {
    // Waiting
  }
  delay(1000);

  Serial.println(F("Falling backward."));
  mip.fallBackward();

  Serial.println();
  Serial.println(F("Sample done."));
}

void loop() {
}
```

---
### fallBackward()
```void fallBackward()```
#### Description
Have the MiP fall backward.

#### Parameters
None

#### Returns
Nothing

#### Example
```c++
#include <mip.h>

MiP     mip;

void setup() {
  bool connectResult = mip.begin();
  if (!connectResult) {
    Serial.println(F("Failed connecting to MiP!"));
    return;
  }

  Serial.println(F("FallDown.ino - Fall forward and backward.\n"));

  Serial.println(F("Waiting for robot to be standing upright."));
  while (!mip.isUpright()) {
    // Waiting
  }
  delay(1000);

  Serial.println(F("Falling forward."));
  mip.fallForward();

  delay(1000);
  Serial.println(F("Waiting for robot to be standing upright again."));
  while (!mip.isUpright()) {
    // Waiting
  }
  delay(1000);

  Serial.println(F("Falling backward."));
  mip.fallBackward();

  Serial.println();
  Serial.println(F("Sample done."));
}

void loop() {
}
```

---
### getUp()
```void getUp(MiPGetUp getup = MIP_GETUP_FROM_EITHER)```
#### Description
Attempt to get the MiP robot back up and balancing after falling to the back or front.

#### Parameters
* **getup** specifies in which direction should the MiP attempt to get up from: **MIP_GETUP_FROM_FRONT**, **MIP_GETUP_FROM_BACK**, or **MIP_GETUP_FROM_EITHER**. MIP_GETUP_FROM_EITHER is the default if this parameter is ommitted.

#### Returns
Nothing

#### Notes
* *I haven't seen my MiP robot actually be successful in accomplishing this operation.*

#### Example
```c++
#include <mip.h>

MiP     mip;

void setup() {
  bool connectResult = mip.begin();
  if (!connectResult) {
    Serial.println(F("Failed connecting to MiP!"));
    return;
  }

  Serial.println(F("GetUp.ino - Use getUp(). Attempt to get up from a front fall."));

  mip.fallForward();
  delay(3000);

  mip.getUp(MIP_GETUP_FROM_FRONT);
  delay(3000);

  Serial.println();
  Serial.println(F("Sample done."));
}

void loop() {
}
```

---
### playSound()
```void playSound(MiPSoundIndex sound, MiPVolume volume = MIP_VOLUME_DEFAULT)```
#### Description
Start playing a single sound immediately. You can use the [beginSoundList()](#beginsoundlist), [addEntryToSoundList()](#addentrytosoundlist), and [playSoundList()](#playsoundlist) functions instead if you want to queue up multiple sounds instead.

#### Parameters
* **sound** is used to specify the index of the sound to be played. The MiPSoundIndex enumeration is described below.
* **volume** is an optional parameter used to set the volume level to be used when playing this sound. If not specified, the volume will remain at its current value.

| MiPSoundIndex |
| ------------- |
| MIP_SOUND_ONEKHZ_500MS_8K16BIT |
| MIP_SOUND_ACTION_BURPING |
| MIP_SOUND_ACTION_DRINKING |
| MIP_SOUND_ACTION_EATING |
| MIP_SOUND_ACTION_FARTING_SHORT |
| MIP_SOUND_ACTION_OUT_OF_BREATH |
| MIP_SOUND_BOXING_PUNCHCONNECT_1 |
| MIP_SOUND_BOXING_PUNCHCONNECT_2 |
| MIP_SOUND_BOXING_PUNCHCONNECT_3 |
| MIP_SOUND_FREESTYLE_TRACKING_1 |
| MIP_SOUND_MIP_1 |
| MIP_SOUND_MIP_2 |
| MIP_SOUND_MIP_3 |
| MIP_SOUND_MIP_APP |
| MIP_SOUND_MIP_AWWW |
| MIP_SOUND_MIP_BIG_SHOT |
| MIP_SOUND_MIP_BLEH |
| MIP_SOUND_MIP_BOOM |
| MIP_SOUND_MIP_BYE |
| MIP_SOUND_MIP_CONVERSE_1 |
| MIP_SOUND_MIP_CONVERSE_2 |
| MIP_SOUND_MIP_DROP |
| MIP_SOUND_MIP_DUNNO |
| MIP_SOUND_MIP_FALL_OVER_1 |
| MIP_SOUND_MIP_FALL_OVER_2 |
| MIP_SOUND_MIP_FIGHT |
| MIP_SOUND_MIP_GAME |
| MIP_SOUND_MIP_GLOAT |
| MIP_SOUND_MIP_GO |
| MIP_SOUND_MIP_GOGOGO |
| MIP_SOUND_MIP_GRUNT_1 |
| MIP_SOUND_MIP_GRUNT_2 |
| MIP_SOUND_MIP_GRUNT_3 |
| MIP_SOUND_MIP_HAHA_GOT_IT |
| MIP_SOUND_MIP_HI_CONFIDENT |
| MIP_SOUND_MIP_HI_NOT_SURE |
| MIP_SOUND_MIP_HI_SCARED |
| MIP_SOUND_MIP_HUH |
| MIP_SOUND_MIP_HUMMING_1 |
| MIP_SOUND_MIP_HUMMING_2 |
| MIP_SOUND_MIP_HURT |
| MIP_SOUND_MIP_HUUURGH |
| MIP_SOUND_MIP_IN_LOVE |
| MIP_SOUND_MIP_IT |
| MIP_SOUND_MIP_JOKE |
| MIP_SOUND_MIP_K |
| MIP_SOUND_MIP_LOOP_1 |
| MIP_SOUND_MIP_LOOP_2 |
| MIP_SOUND_MIP_LOW_BATTERY |
| MIP_SOUND_MIP_MIPPEE |
| MIP_SOUND_MIP_MORE |
| MIP_SOUND_MIP_MUAH_HA |
| MIP_SOUND_MIP_MUSIC |
| MIP_SOUND_MIP_OBSTACLE |
| MIP_SOUND_MIP_OHOH |
| MIP_SOUND_MIP_OH_YEAH |
| MIP_SOUND_MIP_OOPSIE |
| MIP_SOUND_MIP_OUCH_1 |
| MIP_SOUND_MIP_OUCH_2 |
| MIP_SOUND_MIP_PLAY |
| MIP_SOUND_MIP_PUSH |
| MIP_SOUND_MIP_RUN |
| MIP_SOUND_MIP_SHAKE |
| MIP_SOUND_MIP_SIGH |
| MIP_SOUND_MIP_SINGING |
| MIP_SOUND_MIP_SNEEZE |
| MIP_SOUND_MIP_SNORE |
| MIP_SOUND_MIP_STACK |
| MIP_SOUND_MIP_SWIPE_1 |
| MIP_SOUND_MIP_SWIPE_2 |
| MIP_SOUND_MIP_TRICKS |
| MIP_SOUND_MIP_TRIIICK |
| MIP_SOUND_MIP_TRUMPET |
| MIP_SOUND_MIP_WAAAAA |
| MIP_SOUND_MIP_WAKEY |
| MIP_SOUND_MIP_WHEEE |
| MIP_SOUND_MIP_WHISTLING |
| MIP_SOUND_MIP_WHOAH |
| MIP_SOUND_MIP_WOO |
| MIP_SOUND_MIP_YEAH |
| MIP_SOUND_MIP_YEEESSS |
| MIP_SOUND_MIP_YO |
| MIP_SOUND_MIP_YUMMY |
| MIP_SOUND_MOOD_ACTIVATED |
| MIP_SOUND_MOOD_ANGRY |
| MIP_SOUND_MOOD_ANXIOUS |
| MIP_SOUND_MOOD_BORING |
| MIP_SOUND_MOOD_CRANKY |
| MIP_SOUND_MOOD_ENERGETIC |
| MIP_SOUND_MOOD_EXCITED |
| MIP_SOUND_MOOD_GIDDY |
| MIP_SOUND_MOOD_GRUMPY |
| MIP_SOUND_MOOD_HAPPY |
| MIP_SOUND_MOOD_IDEA |
| MIP_SOUND_MOOD_IMPATIENT |
| MIP_SOUND_MOOD_NICE |
| MIP_SOUND_MOOD_SAD |
| MIP_SOUND_MOOD_SHORT |
| MIP_SOUND_MOOD_SLEEPY |
| MIP_SOUND_MOOD_TIRED |
| MIP_SOUND_SOUND_BOOST |
| MIP_SOUND_SOUND_CAGE |
| MIP_SOUND_SOUND_GUNS |
| MIP_SOUND_SOUND_ZINGS |
| MIP_SOUND_SHORT_MUTE_FOR_STOP |
| MIP_SOUND_FREESTYLE_TRACKING_2 |

#### Returns
Nothing

#### Example
```c++
#include <mip.h>

MiP     mip;

void setup() {
  bool connectResult = mip.begin();
  if (!connectResult) {
    Serial.println(F("Failed connecting to MiP!"));
    return;
  }

  Serial.println(F("PlaySound.ino - Play a few sounds."));

  // Play a single sound.
  mip.playSound(MIP_SOUND_ACTION_DRINKING, MIP_VOLUME_4);
  delay(3000);

  // Play 2 sounds with 1 second delay between them, repeating them a second time.
  // Play the first at a lower volume than the second.
  mip.beginSoundList();
  mip.addEntryToSoundList(MIP_SOUND_ACTION_EATING, 1000, MIP_VOLUME_4);
  mip.addEntryToSoundList(MIP_SOUND_ACTION_BURPING, 0, MIP_VOLUME_7);
  mip.playSoundList(1);

  // Play the sound list again after waiting for the previous play to complete.
  delay(10000);
  mip.playSoundList();

  Serial.println();
  Serial.println(F("Sample done."));
}

void loop() {
}
```

---
### beginSoundList()
```void beginSoundList()```
#### Description
Begins the process of having the MiP robot play sounds. After calling beginSoundList(), you can call [addEntryToSoundList()](#addentrytosoundlist) to queue up sounds to play and finally have the queued up sounds start to play by calling [playSoundList()](#playsoundlist).

#### Parameters
None

#### Returns
Nothing

#### Example
```c++
#include <mip.h>

MiP     mip;

void setup() {
  bool connectResult = mip.begin();
  if (!connectResult) {
    Serial.println(F("Failed connecting to MiP!"));
    return;
  }

  Serial.println(F("PlaySound.ino - Play a few sounds."));

  // Play a single sound.
  mip.playSound(MIP_SOUND_ACTION_DRINKING, MIP_VOLUME_4);
  delay(3000);

  // Play 2 sounds with 1 second delay between them, repeating them a second time.
  // Play the first at a lower volume than the second.
  mip.beginSoundList();
  mip.addEntryToSoundList(MIP_SOUND_ACTION_EATING, 1000, MIP_VOLUME_4);
  mip.addEntryToSoundList(MIP_SOUND_ACTION_BURPING, 0, MIP_VOLUME_7);
  mip.playSoundList(1);

  // Play the sound list again after waiting for the previous play to complete.
  delay(10000);
  mip.playSoundList();

  Serial.println();
  Serial.println(F("Sample done."));
}

void loop() {
}
```

---
### addEntryToSoundList()
```void addEntryToSoundList(MiPSoundIndex sound)```<br>
```void addEntryToSoundList(MiPSoundIndex sound, uint16_t delay)```<br>
```void addEntryToSoundList(MiPSoundIndex sound, uint16_t delay, MiPVolume volume)```<br>
#### Description
Adds a sound or volume update entry to the sound list. Before calling addEntryToSoundList(), you must first call [beginSoundList()](#beginsoundlist) and the sounds won't start playing until you call [playSoundList()](#playsoundlist). You can add a maximum of 8 entries to the sound list. Changing the volume levels will use up additional entries so you may actually get less than 8 sounds in the list.

#### Parameters
* **sound** is used to specify the index of the sound to be played for this entry. The MiPSoundIndex enumeration is described below.
* **delay** is an optional parameter used to specify the delay in milliseconds that the MiP should wait after playing this sound before playing the next sound (if any) in the sound list. The granularity of this delay is 30 milliseconds. This parameter defaults to a 0 millisecond delay.
* **volume** is an optional parameter used to set the volume level to be used when playing this sound. If not specified, the volume will remain the same as it was for the previous sound in the list.

| MiPSoundIndex |
| ------------- |
| MIP_SOUND_ONEKHZ_500MS_8K16BIT |
| MIP_SOUND_ACTION_BURPING |
| MIP_SOUND_ACTION_DRINKING |
| MIP_SOUND_ACTION_EATING |
| MIP_SOUND_ACTION_FARTING_SHORT |
| MIP_SOUND_ACTION_OUT_OF_BREATH |
| MIP_SOUND_BOXING_PUNCHCONNECT_1 |
| MIP_SOUND_BOXING_PUNCHCONNECT_2 |
| MIP_SOUND_BOXING_PUNCHCONNECT_3 |
| MIP_SOUND_FREESTYLE_TRACKING_1 |
| MIP_SOUND_MIP_1 |
| MIP_SOUND_MIP_2 |
| MIP_SOUND_MIP_3 |
| MIP_SOUND_MIP_APP |
| MIP_SOUND_MIP_AWWW |
| MIP_SOUND_MIP_BIG_SHOT |
| MIP_SOUND_MIP_BLEH |
| MIP_SOUND_MIP_BOOM |
| MIP_SOUND_MIP_BYE |
| MIP_SOUND_MIP_CONVERSE_1 |
| MIP_SOUND_MIP_CONVERSE_2 |
| MIP_SOUND_MIP_DROP |
| MIP_SOUND_MIP_DUNNO |
| MIP_SOUND_MIP_FALL_OVER_1 |
| MIP_SOUND_MIP_FALL_OVER_2 |
| MIP_SOUND_MIP_FIGHT |
| MIP_SOUND_MIP_GAME |
| MIP_SOUND_MIP_GLOAT |
| MIP_SOUND_MIP_GO |
| MIP_SOUND_MIP_GOGOGO |
| MIP_SOUND_MIP_GRUNT_1 |
| MIP_SOUND_MIP_GRUNT_2 |
| MIP_SOUND_MIP_GRUNT_3 |
| MIP_SOUND_MIP_HAHA_GOT_IT |
| MIP_SOUND_MIP_HI_CONFIDENT |
| MIP_SOUND_MIP_HI_NOT_SURE |
| MIP_SOUND_MIP_HI_SCARED |
| MIP_SOUND_MIP_HUH |
| MIP_SOUND_MIP_HUMMING_1 |
| MIP_SOUND_MIP_HUMMING_2 |
| MIP_SOUND_MIP_HURT |
| MIP_SOUND_MIP_HUUURGH |
| MIP_SOUND_MIP_IN_LOVE |
| MIP_SOUND_MIP_IT |
| MIP_SOUND_MIP_JOKE |
| MIP_SOUND_MIP_K |
| MIP_SOUND_MIP_LOOP_1 |
| MIP_SOUND_MIP_LOOP_2 |
| MIP_SOUND_MIP_LOW_BATTERY |
| MIP_SOUND_MIP_MIPPEE |
| MIP_SOUND_MIP_MORE |
| MIP_SOUND_MIP_MUAH_HA |
| MIP_SOUND_MIP_MUSIC |
| MIP_SOUND_MIP_OBSTACLE |
| MIP_SOUND_MIP_OHOH |
| MIP_SOUND_MIP_OH_YEAH |
| MIP_SOUND_MIP_OOPSIE |
| MIP_SOUND_MIP_OUCH_1 |
| MIP_SOUND_MIP_OUCH_2 |
| MIP_SOUND_MIP_PLAY |
| MIP_SOUND_MIP_PUSH |
| MIP_SOUND_MIP_RUN |
| MIP_SOUND_MIP_SHAKE |
| MIP_SOUND_MIP_SIGH |
| MIP_SOUND_MIP_SINGING |
| MIP_SOUND_MIP_SNEEZE |
| MIP_SOUND_MIP_SNORE |
| MIP_SOUND_MIP_STACK |
| MIP_SOUND_MIP_SWIPE_1 |
| MIP_SOUND_MIP_SWIPE_2 |
| MIP_SOUND_MIP_TRICKS |
| MIP_SOUND_MIP_TRIIICK |
| MIP_SOUND_MIP_TRUMPET |
| MIP_SOUND_MIP_WAAAAA |
| MIP_SOUND_MIP_WAKEY |
| MIP_SOUND_MIP_WHEEE |
| MIP_SOUND_MIP_WHISTLING |
| MIP_SOUND_MIP_WHOAH |
| MIP_SOUND_MIP_WOO |
| MIP_SOUND_MIP_YEAH |
| MIP_SOUND_MIP_YEEESSS |
| MIP_SOUND_MIP_YO |
| MIP_SOUND_MIP_YUMMY |
| MIP_SOUND_MOOD_ACTIVATED |
| MIP_SOUND_MOOD_ANGRY |
| MIP_SOUND_MOOD_ANXIOUS |
| MIP_SOUND_MOOD_BORING |
| MIP_SOUND_MOOD_CRANKY |
| MIP_SOUND_MOOD_ENERGETIC |
| MIP_SOUND_MOOD_EXCITED |
| MIP_SOUND_MOOD_GIDDY |
| MIP_SOUND_MOOD_GRUMPY |
| MIP_SOUND_MOOD_HAPPY |
| MIP_SOUND_MOOD_IDEA |
| MIP_SOUND_MOOD_IMPATIENT |
| MIP_SOUND_MOOD_NICE |
| MIP_SOUND_MOOD_SAD |
| MIP_SOUND_MOOD_SHORT |
| MIP_SOUND_MOOD_SLEEPY |
| MIP_SOUND_MOOD_TIRED |
| MIP_SOUND_SOUND_BOOST |
| MIP_SOUND_SOUND_CAGE |
| MIP_SOUND_SOUND_GUNS |
| MIP_SOUND_SOUND_ZINGS |
| MIP_SOUND_SHORT_MUTE_FOR_STOP |
| MIP_SOUND_FREESTYLE_TRACKING_2 |

#### Returns
Nothing

#### Example
```c++
#include <mip.h>

MiP     mip;

void setup() {
  bool connectResult = mip.begin();
  if (!connectResult) {
    Serial.println(F("Failed connecting to MiP!"));
    return;
  }

  Serial.println(F("PlaySound.ino - Play a few sounds."));

  // Play a single sound.
  mip.playSound(MIP_SOUND_ACTION_DRINKING, MIP_VOLUME_4);
  delay(3000);

  // Play 2 sounds with 1 second delay between them, repeating them a second time.
  // Play the first at a lower volume than the second.
  mip.beginSoundList();
  mip.addEntryToSoundList(MIP_SOUND_ACTION_EATING, 1000, MIP_VOLUME_4);
  mip.addEntryToSoundList(MIP_SOUND_ACTION_BURPING, 0, MIP_VOLUME_7);
  mip.playSoundList(1);

  // Play the sound list again after waiting for the previous play to complete.
  delay(10000);
  mip.playSoundList();

  Serial.println();
  Serial.println(F("Sample done."));
}

void loop() {
}
```

---
### playSoundList()
```void playSoundList(uint8_t repeatCount = 0)```
#### Description
Starts playing the entries found in the sound list. Before you call playSoundList(), the sound list must have been initialized and populated with calls to [beginSoundList()](#beginsoundlist) and [addEntryToSoundList()](#addentrytosoundlist).

#### Parameters
* **repeatCount** is an optional parameter which specifies the number of times that the entries in the sound list should be repeated (0 - 255). A value of 0 means that the sound list will play once and then stop whereas a value of 1 means that it would play the sequence a total of 2 times. The default value for this parameter is 0 additional repeats.

#### Returns
Nothing

#### Example
```c++
#include <mip.h>

MiP     mip;

void setup() {
  bool connectResult = mip.begin();
  if (!connectResult) {
    Serial.println(F("Failed connecting to MiP!"));
    return;
  }

  Serial.println(F("PlaySound.ino - Play a few sounds."));

  // Play a single sound.
  mip.playSound(MIP_SOUND_ACTION_DRINKING, MIP_VOLUME_4);
  delay(3000);

  // Play 2 sounds with 1 second delay between them, repeating them a second time.
  // Play the first at a lower volume than the second.
  mip.beginSoundList();
  mip.addEntryToSoundList(MIP_SOUND_ACTION_EATING, 1000, MIP_VOLUME_4);
  mip.addEntryToSoundList(MIP_SOUND_ACTION_BURPING, 0, MIP_VOLUME_7);
  mip.playSoundList(1);

  // Play the sound list again after waiting for the previous play to complete.
  delay(10000);
  mip.playSoundList();

  Serial.println();
  Serial.println(F("Sample done."));
}

void loop() {
}
```

---
### writeVolume()
```void writeVolume(uint8_t volume)```
#### Description
Set the MiP robot's volume level.

#### Parameters
* **volume** is the new volume level (0 - 7).  A level of 0 turns off the sound and 7 is the loudest setting.

#### Returns
Nothing

#### Example
```c++
#include <mip.h>

MiP     mip;

void setup() {
  bool connectResult = mip.begin();
  if (!connectResult) {
    Serial.println(F("Failed connecting to MiP!"));
    return;
  }

  Serial.println(F("Volume.ino - Use read/writeVolume(). Set volume level to 1 and read out afterwards."));

  mip.writeVolume(1);

  uint8_t volume = mip.readVolume();

  Serial.print(F("Volume = "));
    Serial.println(volume);

  Serial.println();
  Serial.println(F("Sample done."));
}

void loop() {
}
```

---
### readVolume()
```uint8_t readVolume()```
#### Description
Read the MiP robot's current volume level setting.

#### Parameters
None

#### Returns
The current volume level (0 - 7).  A level of 0 means the sound is off and 7 is the loudest setting.

#### Example
```c++
#include <mip.h>

MiP     mip;

void setup() {
  bool connectResult = mip.begin();
  if (!connectResult) {
    Serial.println(F("Failed connecting to MiP!"));
    return;
  }

  Serial.println(F("Volume.ino - Use read/writeVolume(). Set volume level to 1 and read out afterwards."));

  mip.writeVolume(1);

  uint8_t volume = mip.readVolume();

  Serial.print(F("Volume = "));
    Serial.println(volume);

  Serial.println();
  Serial.println(F("Sample done."));
}

void loop() {
}
```

---
### readDistanceTravelled()
```float readDistanceTravelled()```
#### Description
Read the current MiP odometer tally.

#### Parameters
None

#### Returns
The distance travelled (in centimeters) since the last reset.

#### Notes
* The MiP robot's odometer is similar to that in a car.  It maintains the total tally of the distance travelled, even across power cycles.
* The [resetDistanceTravelled()](#resetdistancetravelled) function can be used to reset the odometer.

#### Example
```c++
#include <mip.h>

MiP     mip;

void setup() {
  bool connectResult = mip.begin();
  if (!connectResult) {
    Serial.println(F("Failed connecting to MiP!"));
    return;
  }

  Serial.println(F("Odometer.ino - Read out current odometer reading and reset."));

  float cm = mip.readDistanceTravelled();
  Serial.print(F("MiP has travelled "));
    Serial.print(cm);
    Serial.println(F(" cm since the last reset."));

  mip.resetDistanceTravelled();

  Serial.println();
  Serial.println(F("Sample done."));
}

void loop() {
}
```

---
### resetDistanceTravelled()
```void  resetDistanceTravelled()```
#### Description
Reset the MiP robot's odometer. The current odometer distance measurement is available by calling the [readDistanceTravelled()](#readdistancetravelled) function.

#### Parameters
None

#### Returns
Nothing

#### Notes
* The MiP robot's odometer doesn't automatically reset during a power cycle.
* You should call this function if you want to manually reset it.

#### Example
```c++
#include <mip.h>

MiP     mip;

void setup() {
  bool connectResult = mip.begin();
  if (!connectResult) {
    Serial.println(F("Failed connecting to MiP!"));
    return;
  }

  Serial.println(F("Odometer.ino - Read out current odometer reading and reset."));

  float cm = mip.readDistanceTravelled();
  Serial.print(F("MiP has travelled "));
    Serial.print(cm);
    Serial.println(F(" cm since the last reset."));

  mip.resetDistanceTravelled();

  Serial.println();
  Serial.println(F("Sample done."));
}

void loop() {
}
```

---
### readBatteryVoltage()
```float readBatteryVoltage()```
#### Description
Read the MiP robot's current battery level.

#### Parameters
None

#### Returns
The current battery voltage in Volts.

#### Notes
* The MiP robot status updates, which include the battery level, may be lost if you are spending too much time sending output back to the Arduino IDE's serial monitor. See [Limitations](#limitations) section above.
* These status updates are usually sent every 30 seconds or earlier if the MiP detects a change in position.

#### Example
```c++
#include <mip.h>

MiP     mip;

void setup() {
  bool connectResult = mip.begin();
  if (!connectResult) {
    Serial.println(F("Failed connecting to MiP!"));
    return;
  }

  Serial.println(F("Status.ino - Display MiP status as it changes."));
}

void loop() {
  static float       lastBatteryLevel = 0.0f;
  static MiPPosition lastPosition = (MiPPosition) - 1;

  float              currentBatteryLevel = mip.readBatteryVoltage();
  MiPPosition        currentPosition = mip.readPosition();

  if (currentBatteryLevel != lastBatteryLevel) {
    Serial.print(F("Battery: "));
      Serial.print(currentBatteryLevel);
      Serial.println(F("V"));
    lastBatteryLevel = currentBatteryLevel;
  }

  if (currentPosition != lastPosition) {
    if (mip.isOnBack()) {
      Serial.println(F("Position: On Back"));
    }
    if (mip.isFaceDown()) {
      Serial.println(F("Position: Face Down"));
    }
    if (mip.isUpright()) {
      Serial.println(F("Position: Upright"));
    }
    if (mip.isPickedUp()) {
      Serial.println(F("Position: Picked Up"));
    }
    if (mip.isHandStanding()) {
      Serial.println(F("Position: Hand Stand"));
    }
    if (mip.isFaceDownOnTray()) {
      Serial.println(F("Position: Face Down on Tray"));
    }
    if (mip.isOnBackWithKickstand()) {
      Serial.println(F("Position: On Back With Kickstand"));
    }

    lastPosition = currentPosition;
  }
}
```

---
### readPosition()
```MiPPosition readPosition()```
#### Description
Read the MiP robot's current position.

#### Parameters
None

#### Returns
One of the values from the following table:

| MiPPosition Value |
| ----------------- |
| MIP_POSITION_ON_BACK |
| MIP_POSITION_FACE_DOWN |
| MIP_POSITION_UPRIGHT |
| MIP_POSITION_PICKED_UP |
| MIP_POSITION_HAND_STAND |
| MIP_POSITION_FACE_DOWN_ON_TRAY |
| MIP_POSITION_ON_BACK_WITH_KICKSTAND |

#### Notes
* The MiP robot status updates, which include the position, may be lost if you are spending too much time sending output back to the Arduino IDE's serial monitor. See [Limitations](#limitations) section above.
* These status updates are usually sent every 30 seconds or earlier if the MiP detects a change in position.

#### Example
```c++
#include <mip.h>

MiP     mip;

void setup() {
  bool connectResult = mip.begin();
  if (!connectResult) {
    Serial.println(F("Failed connecting to MiP!"));
    return;
  }

  Serial.println(F("Status.ino - Display MiP status as it changes."));
}

void loop() {
  static float       lastBatteryLevel = 0.0f;
  static MiPPosition lastPosition = (MiPPosition) - 1;

  float              currentBatteryLevel = mip.readBatteryVoltage();
  MiPPosition        currentPosition = mip.readPosition();

  if (currentBatteryLevel != lastBatteryLevel) {
    Serial.print(F("Battery: "));
      Serial.print(currentBatteryLevel);
      Serial.println(F("V"));
    lastBatteryLevel = currentBatteryLevel;
  }

  if (currentPosition != lastPosition) {
    if (mip.isOnBack()) {
      Serial.println(F("Position: On Back"));
    }
    if (mip.isFaceDown()) {
      Serial.println(F("Position: Face Down"));
    }
    if (mip.isUpright()) {
      Serial.println(F("Position: Upright"));
    }
    if (mip.isPickedUp()) {
      Serial.println(F("Position: Picked Up"));
    }
    if (mip.isHandStanding()) {
      Serial.println(F("Position: Hand Stand"));
    }
    if (mip.isFaceDownOnTray()) {
      Serial.println(F("Position: Face Down on Tray"));
    }
    if (mip.isOnBackWithKickstand()) {
      Serial.println(F("Position: On Back With Kickstand"));
    }

    lastPosition = currentPosition;
  }
}
```

---
### isOnBack()
```bool  isOnBack()```
#### Description
Is the MiP robot currently lying on its back?

#### Parameters
None

#### Returns
* **true** if the MiP robot is currently lying on its back.
* **false** otherwise.

#### Notes
* The MiP robot status updates, which include the position, may be lost if you are spending too much time sending output back to the Arduino IDE's serial monitor. See [Limitations](#limitations) section above.
* These status updates are usually sent every 30 seconds or earlier if the MiP detects a change in position.

#### Example
```c++
#include <mip.h>

MiP     mip;

void setup() {
  bool connectResult = mip.begin();
  if (!connectResult) {
    Serial.println(F("Failed connecting to MiP!"));
    return;
  }

  Serial.println(F("Status.ino - Display MiP status as it changes."));
}

void loop() {
  static float       lastBatteryLevel = 0.0f;
  static MiPPosition lastPosition = (MiPPosition) - 1;

  float              currentBatteryLevel = mip.readBatteryVoltage();
  MiPPosition        currentPosition = mip.readPosition();

  if (currentBatteryLevel != lastBatteryLevel) {
    Serial.print(F("Battery: "));
      Serial.print(currentBatteryLevel);
      Serial.println(F("V"));
    lastBatteryLevel = currentBatteryLevel;
  }

  if (currentPosition != lastPosition) {
    if (mip.isOnBack()) {
      Serial.println(F("Position: On Back"));
    }
    if (mip.isFaceDown()) {
      Serial.println(F("Position: Face Down"));
    }
    if (mip.isUpright()) {
      Serial.println(F("Position: Upright"));
    }
    if (mip.isPickedUp()) {
      Serial.println(F("Position: Picked Up"));
    }
    if (mip.isHandStanding()) {
      Serial.println(F("Position: Hand Stand"));
    }
    if (mip.isFaceDownOnTray()) {
      Serial.println(F("Position: Face Down on Tray"));
    }
    if (mip.isOnBackWithKickstand()) {
      Serial.println(F("Position: On Back With Kickstand"));
    }

    lastPosition = currentPosition;
  }
}
```

---
### isFaceDown()
```bool  isFaceDown()```
#### Description
Is the MiP robot currently lying on its front?

#### Parameters
None

#### Returns
* **true** if the MiP robot is currently lying on its front.
* **false** otherwise.

#### Notes
* The MiP robot status updates, which include the position, may be lost if you are spending too much time sending output back to the Arduino IDE's serial monitor. See [Limitations](#limitations) section above.
* These status updates are usually sent every 30 seconds or earlier if the MiP detects a change in position.
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

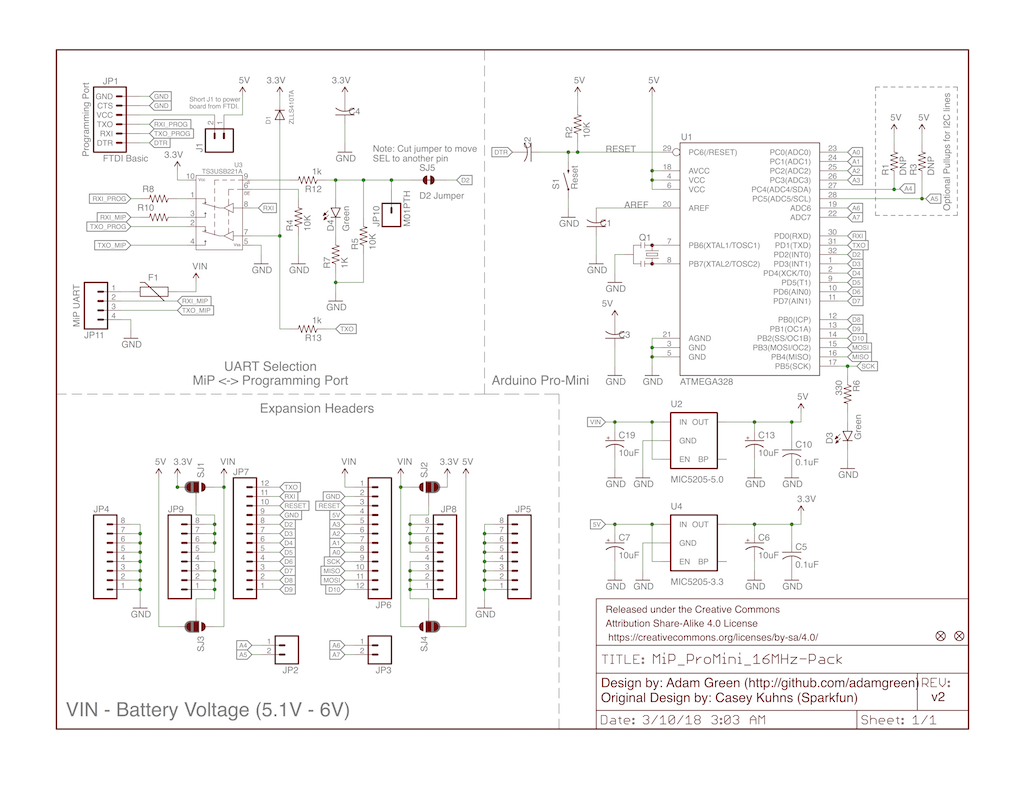
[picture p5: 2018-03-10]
images/20180310-Schematic.png

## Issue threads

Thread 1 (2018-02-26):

Project kickoff

adamgreen, 2018-02-26:
I started this project in response to [this issue](https://github.com/WowWeeLabs/MiP-BLE-Protocol/issues/18). This issue concerns the fact that the [Sparkfun MiP ProMini-Pack](https://www.sparkfun.com/products/retired/13058) running at 8MHz/3.3V can't reliably receive 115200 bps serial data from the MiP.

I am opening this issue to open a dialog with @Tiogaplanet and anyone else that might be interested in this attempt to produce an updated version of the board running at 16MHz/5V.

### Progress So Far
* I have committed a first draft of the changes that I want to make to the schematic:
  * Bumps the clock rate up to 16MHz and the voltage up to 5V (5V needed for AVR to run reliably at 16 MHz).
  * By default I no longer connect the FTDI header's VCC pin to anything. I have never liked that both it and the MiP battery could be powering the board at the same time with no diode protection in place. There are also some FTDI adapters out there that supply 3.3V on this pin while most supply 5V. If the user has a 5V FTDI adapter and want to power the board from it then they can short the 2 pins of J1.
  * The TS3USB221A switch is still powered at 3.3V. I added 1k ohm current limiting resistors to its inputs and also added a Schottky diode for 5V->3.3V level conversion on the TXO pin.
  * I cascaded the 3.3V regulator off of the 5V supply so that the board will work if powered from the FTDI cable.
  *  ~~Added an AVR ISP header to make it easier for me to get the Arduino compatible bootloader initially loaded into the ATMEGA328. My plan is to place this on the back of the board and use a temporary pogo pin connection instead of soldering in a bulky header that would interfere with the battery pack. Would want to do this bootloader programming before C2 is installed on the RESET line since it will cause the programming to fail otherwise.~~
* I haven't done any work on updating the PCB layout yet. I want to feel like we have finalized the schematic updates before starting the layout.

@Tiogaplanet I would appreciate any feedback you have on the schematic changes made so far. Anything else you think I should address? All feedback welcome!

Tiogaplanet, 2018-02-27:
@adamgreen This is great news!  Glad to see this project and thanks to you for starting it.

I was never able to get enough of the original board working to really constructively criticize its features.  I'd be happy with the changes you've described above and then making sure we can get a functioning library to run on it before considering other changes.  Do you plan on keeping the room onboard to add headers?  I was looking forward to employing those to be able to add even minor functionality to the MiP.

adamgreen, 2018-02-27:
> Do you plan on keeping the room onboard to add headers? I was looking forward to employing those to be able to add even minor functionality to the MiP.

Yes, but I switched all of the Vcc (3.3V) pads to 5V. Should I expose the 3.3V supply as well? **JP8** and **JP9** allow you to select between 5V and Vin (~6V) but are split so that you can have one of those voltages on the bottom half and the other on the top. I could modify the bottom jumpers so that they select between 3.3V and Vin instead. What do you think?

adamgreen, 2018-03-01:
With commit dcafb2c, 3.3V is now exposed on the lower half of the two vertical power buses in the prototyping area of the board.

adamgreen, 2018-03-10:
I have placed an order with [OSHPark](https://www.oshpark.com) to have the new version of this board produced. Here are previews downloaded from OSHPark:

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

Tiogaplanet, 2018-03-11:
@adamgreen It looks great!  I can't wait to have another go at this.

I'm on travel right now and for most of March, hence my silence.  But I can't wait to see how this all turns out.

adamgreen, 2018-03-11:
@Tiogaplanet There is a good chance I probably won't get back to it until early April either since it will take a few weeks to get the boards back and by then I too will be traveling. I hope your travels go well.

I will reply back here again once I get the new board populated and tested.

adamgreen, 2018-04-16:
@Tiogaplanet I just wanted to update you on my latest status. The new PCBs arrived from OSHPark while I was traveling and I just got around to soldering them up last week. So far the new PCB design appears to be working well. I did find one issue with the 3.3V supply that I will investigate a bit more but I already hacked the current PCB to work around that issue for now so that I can continue testing. I did verify that this version of the PCB can reliably read the software version out of the MiP via the UART @115200.

I will port my existing [MiP-Capi](https://github.com/adamgreen/MiP-Capi) library to the Arduino and use it to conduct more thorough testing this week.

Here is a photo of the new PCB mounted on my MiP.<br>
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

I created a custom jig to allow me to program the Arduino compatible bootloader into the AVR. This only needs to be done once and then it can be programmed via the Arduino IDE.<br>
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

Tiogaplanet, 2018-04-17:
@adamgreen That looks great! Are you ready or willing to ship? If so, I'd love to continue trying to develop my own library.  I'd offer assistance with yours but I doubt you need it.

adamgreen, 2018-04-17:
@Tiogaplanet There are a few problems with this version of the PCB that I plan to correct in the near future. So far there isn't anything major and I have been able to work around them. I could wait and build up one of the corrected PCBs or I could populate another of these and send it to you. It's up to you.

As for the library, I was planning to finish porting & testing my [C API](https://github.com/adamgreen/MiP-Capi#readme) in the Arduino IDE. Currently it has 2 layers. The high level MiP protocol exposed to developers and an underlying transport abstraction. Once I have that working, I was thinking that I would merge the 2 layers for the Arduino version. The code is already kind of object oriented so I would just complete that by turning it into a C++ class. It wouldn't be in the style expected for Arduino libraries though.

How would your library differ from mine or the existing Sparkfun one? Do you just want to take what I end up with and finish turning it into something more comparable to other Arduino libraries?

adamgreen, 2018-04-17:
>I'm sure I can wait until you have a finished product.

Ok, let me finish my current porting/testing and then we can decide once I have a better handle on all of the issues in the current design. Sending you one of the current versions gets you a board to play with earlier but sending you the revised version means that the final board design as found on GitHub will get more test coverage.

> I don't have my heart set on any particular implementation as long as I or a kid can quickly put a sketch together and have the MiP do something, even if the action is basic.

Once I finish my current port, you can take a look at it to see if you want to:
*  Contribute changes back to it which Arduinize and/or simplify it.
* Just pull code from it to create your own MiP library.
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
adamgreen, 2018-05-11:
@Tiogaplanet Thanks for the great feedback! Much appreciated. It sounds like once you start writing sketches again for your MiP, you can probably use my Arduino library as your starting point instead of the Sparkfun one. That would be great!

> Once I resume writing sketches for the MiP I can offer informed feedback but I do have a few initial impressions.

👍
I agree. All the more reason I need to get these boards soldered up and sent off to you! :)

>I like the ability to play a list of sounds. I would not have thought of implementing such a thing. On the flip side, I'd still like a simple playSound function that just plays a single iteration of whatever enumerated sound value is passed to it.

I agree.

> I don't see any setGame functions but I may have overlooked them.

You are correct. I didn't implement that functionality but it could be added.

> How about implementing a disconnect per the Wowwee API, in addition to having the end function in your API?

I just used the begin()/end() nomenclature since it is so common in other Arduino libraries. In actuality, I don't ever call end() in my samples since it is such a pain to get it out of sleep mode (need to power cycle the bot after uploading new code). Maybe end() should be switched to use disconnect instead and have a separate API for putting the MiP to sleep?

> My own struggles with reading the software version using the original Sparkfun board had me implementing cache variables for reads that never or seldom change. Software version and hardware version never change so there is no reason to clobber the serial connection once you've read the version numbers once.

But on the flip side, you shouldn't be asking for the software/hardware version so often that it is worth caching. However if you didn't want to return the version information in a structure but instead have separate calls to pull out each piece (year, month, day, etc) then it would make sense to cache in that case.

> Same thinking applies for doing multiple gets with no set in between.

That might be the case. Once you start using the library to write your own sketches, you might hit performance bottlenecks and that will put the spotlight on where we should make such optimizations. I should mention that I traded off performance a bit to make the library more robust by doing almost the opposite: I often issue  a get as part of the corresponding set to make sure that the set actually got through since the MiP does sometimes ignore requests and it has no acknowledge for sets. I tried to make the library as robust as possible with error detection and retry logic so that the user wouldn't need to.

Once you start using the library, you can enter issues here and then we can figure out if you want to fix and send a PR or if I should attempt to make the fix instead. Even for the above mentioned items (```playSound()```, ```setGame()```, ```disconnect```, ...) would you prefer to make those changes once you start using the library or would you prefer for me to work on them?

Thanks again for everything!

adamgreen, 2018-06-06:
> All the more reason I need to get these boards soldered up and sent off to you! :)

@Tiogaplanet, I am happy to hear that you have received these boards. Sorry it took so long for me to get everything ready and sent off to you. I can't wait to see your feedback and updates! Best of luck!

Tiogaplanet, 2018-06-08:
Soldered a header on last night and ran SRSdemo.  Worked perfectly first time around.

Will spend some time coding this weekend.  I'm thinking of writing some kind of program to exercise everything you've already implemented.  Let's see how far I get.....

adamgreen, 2018-06-08:
Excellent!

2stacks, 2018-06-30:
@adamgreen great work! I like @tiogaplanet never gave up working on my MiP.  Id love to be involved and help out if I can.

adamgreen, 2018-06-30:
> @adamgreen great work!

Thanks! @Tiogaplanet did a lot of the preliminary investigation that lead to the kickoff of this project as well and then helped verify my work!

> I like @Tiogaplanet never gave up working on my MiP.

That's awesome to hear! What kind of projects have you been doing with your MiP?

> Id love to be involved and help out if I can.

Sounds great! Take a look around the current project and let me know what areas you would like to help with.

adamgreen, 2018-07-01:
Since the initial version of this project is now available, I am thinking that I should soon close up this **kickoff** issue. We can now open issues that are specific to the issues and/or features that we would still like to see addressed. Any objections?

adamgreen, 2018-07-01:
Excellent!

Thanks again for helping out with the kick-off!

Closed 2019-03-26.

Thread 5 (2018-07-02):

Switch end() to just disconnect and add sleep() for old functionality

adamgreen, 2018-07-02:
It make sense to have the existing end() function use the new disconnect functionality and expose the old behavior via a new sleep() method.

I will work on this change.

adamgreen, 2018-07-03:
Fix committed to GitHub.

Closed 2018-07-03.

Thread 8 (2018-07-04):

Implement getUserData() and setUserData()

Tiogaplanet, 2018-07-04:
This functionality would be useful for storing variables across power cycles on the MiP.  It could also be used to transfer data between Arduino sketches and Bluetooth apps.

I've started the work, shown in my latest [commit](https://github.com/Tiogaplanet/MiP_ProMini-Pack/commit/9af15418eb187bd17ac02f5edae94ee9a6b7fd4f).  It's not working quite right and I think the problem is in one of the lower transport levels.  My output from ReadWriteEeprom.ino looks like this:

```
ReadWriteEeprom.ino - Writes data to EEPROM and reads it back.
MiP: Bad OOB command byte: 0 (discarded 0 bytes)
MiP: Bad OOB command byte: 0 (discarded 2 bytes)
MiP: Response timeout
Scrambled password: 0
Recovered password: 0
```

Will resume writing/debugging tomorrow.

Tiogaplanet, 2018-07-04:
OK, I'm really done for tonight now.  I got a little closer to the bullseye with this [commit](https://github.com/Tiogaplanet/MiP_ProMini-Pack/commit/0886da0feea6aaa65d9777bbed81773f051c5148).

My output now looks like this:

```
ReadWriteEeprom.ino - Writes data to EEPROM and reads it back.
Original password: 10
Scrambled password: 255
Recovered password: 32
```

adamgreen, 2018-07-07:
Implemented as of PR #9

Closed 2018-07-07.

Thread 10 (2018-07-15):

Enable IR support in library

Tiogaplanet, 2018-07-15:
I'm creating this issue to track my progress on enabling IR support.  I've started by trying to send and receive IR dongle code.  I think this needs IR remote control enabled to work but I can't tell for sure after reviewing WowWee's documentation.  Right now my recieveIRDongleCode() goes into an infinite loop of MiP timeout error messages.  I need to fix it up so that if there are no dongle codes waiting, then exit quietly.  I suspect the implementation needs to look like reading gesture or radar events.

Anyway, I've gotten as far as I'll get tonight.  My latest [commit is posted](https://github.com/Tiogaplanet/MiP_ProMini-Pack/commit/1effcb8fca9e875bdf8eff27e97cfb05eab19623).

adamgreen, 2018-07-15:
>  I suspect the implementation needs to look like reading gesture or radar events.

If it needs to be treated like gestures and radar events then you should see the **"MiP: Bad OOB command byte:"** error from [here](https://github.com/adamgreen/MiP_ProMini-Pack/blob/master/Arduino/MiP_ProMini_Pack_Library/src/mip.cpp#L2132) being logged to the serial port.

Tiogaplanet, 2018-07-20:
Another weekend, another chance to get IR working.

Coded up the detection mode functions.  Still need to test, debug, tidy up the code, document everything, etc.  This is just an incremental [commit](https://github.com/Tiogaplanet/MiP_ProMini-Pack/commit/aff7b524b3af7afd90d4f4839e915037b308dc68).

adamgreen, 2018-07-21:
Best of luck! It will be very cool to have this additional feature in the library.

Tiogaplanet, 2018-07-21:
I am able to get both mips to detect each other and pass their user-defined IDs.  I am also able to turn IR remote control on and off but it's useless without knowing what IR codes to send.  I've got a hard-to-find bug in sending and receiving IR dongle code.  Of course, because that's the most useful part of all the IR stuff.  No commit right now.  May resume work later today or tomorrow.

Tiogaplanet, 2018-07-22:
Some notes for myself before I start putting together a PR.

Enabling and disabling detection mode works.  Enabling it allows MiP to start receiving MiP detected
messages (0x04).  Requesting MiP detection status (0x0F) does not work.  Sending a 0x0F does NOT get a 0x0F in return.  So there's no reasons to do (enable|disable)MiPDetectionMode()->verifiedMiPDetectionMode()->rawSetDetectionMode().  Rather, just go straight to (enable|disable)MiPDetectionMode()->rawSetDetectionMode()

Sending and receiving dongle code works.

Enabling and disabling IR remote control works but am unable to test.

Tiogaplanet, 2018-07-22:
I've settled on three discrete sections to implement here.

1. MiP detection

- enableMiPDetectionMode() allows MiP to be discovered by another MiP.
- disableMiPDetectionMode() prevents MiP from being discovered.
- isMiPDetectionModeEnabled() is a checker.
- readDetectedMiP() is an event reader that reports the last discovered MiP.

2. IR remote control

- enableIRRemoteControl() seems to work, no way to test, yet.
- disableIRRemoteControl() seems to work.
- isIRRemoteControlEnabled() is a checker.

3. Sending and receiving IR dongle code

- sendIRDongleCode() seems to work.
- readIRDongleCode() is the thing that is holding everything up.  It's buggy.  According to WowWee's UART command list a 0x04 command could be three to five bytes long.  It's the only command that has a variable length so implementing it is tricky.  I've tried varying the length of the buffer by reading two nibbles and doing the shifting and hex conversion similar to what's done to determine commandByte.  But I end up losing the first byte of the transmitted data.  For example, sending a { 0x01, 0x02, 0x03, 0x04 } produces { 0x00, 0x02, 0x03, 0x04 } on the receiving end.

Taking a short break but latest [commit](https://github.com/adamgreen/MiP_ProMini-Pack/compare/master...Tiogaplanet:Infrared) is posted.

Tiogaplanet, 2018-07-22:
When sending 2 or 3 bytes everything works fine.

```
sender: { 0x01, 0x02, 0x03, 0x04 }, two bytes are valid   -> recipient: { 0x03, 0x04 }
sender: { 0x01, 0x02, 0x03, 0x04 }, three bytes are valid -> recipient: { 0x02, 0x03, 0x04 }
```
This is where the problem starts:
```
sender: { 0x01, 0x02, 0x03, 0x04 }, four bytes are valid -> recipient: { 0x00, 0x02, 0x03, 0x04 }
```

I'm not sure why a zero is getting returned when I try sending four bytes.  @adamgreen if you've got any ideas I'd love to hear them.  I think this is going to stump me for a while.

adamgreen, 2018-07-22:
@Tiogaplanet I added a comment to your latest commit about one buffer overrun bug I see that could cause the corruption that you are reporting here.

adamgreen, 2018-07-22:
For the remote control enabling stuff that you can't test, I would add those functions to the library as you have but probably not document them and leave out the examples. If someone later figures out what to do with them, then they/we can write examples and documentation at that time.

Tiogaplanet, 2018-07-23:
I made the buffer 4 * 2 and I printed the contents of the buffer right after reading it.  When sending { 0x01, 0x02, 0x03, 0x04 } the buffer on the receiving end contains:

4848485048514852

4848 is 0, 4850 is 2, 4851 is 3 and 4852 is 4

Maybe MiP sends the sendIRDongle out of the order in which it gets written to the UART?  If so, is there a send buffer somewhere that is too small?

adamgreen, 2018-07-23:
It almost looks like the MiP only sends over 20 bits at maximum. If that was the case then you should get results like this:

Length (bits) | Data Sent | Data Received
-|-|-
32 | 0xFF, 0xFF, 0xFF, 0xFF | 0x00, 0x0F, 0xFF, 0xFF
24 | 0xFF, 0xFF, 0xFF | 0x0F, 0xFF, 0xFF

Tiogaplanet, 2018-07-24:
That's entirely possible.  I don't know the order that MiP sends the data via IR.  I only know the order that it's transmitted to the promini via UART (command, data numbers, data, data, data, data) on the receiving end.

The funny thing is, MiP will only send command 0x8C if byte five is 0x10, 0x18 or 0x20 which leads me to believe that it's expecting to send four data bytes.  Also, I noted in my experiments that 0x8C will not send if byte five is 0x08 as indicated in the @WowWeeLabs' [command document](https://raw.githubusercontent.com/WowWeeLabs/MiP-BLE-Protocol/master/MiP-Protocol.md).

So at this point I am questioning whether or not `sendIRDongle()` code is working correctly.  I may have to pick up an IR sensor and turn my Arduino Uno clone into a decoder using some of the guides I've seen online to make sure I'm actually sending the correct data string.

If I can't figure this out soon, would you be willing to add this to your library with the limitation of only sending two or three bytes via IR while I continue to debug sending a fourth byte?

adamgreen, 2018-07-24:
> I don't know the order that MiP sends the data via IR.

The one thing that the documentation does mention is that the UART data is in big endian order. The documentation implies that you are really sending so many bits out of a uint32_t value (not really an array of 4-bytes) with the most significant byte coming first in the UART data. So if you ask it to send 16 bits, then it should send the last two bytes of the UART data section and not the first two bytes.

> The funny thing is, MiP will only send command 0x8C if byte five is 0x10, 0x18 or 0x20 which leads me to believe that it's expecting to send four data bytes.

Which also agrees with the fact that the receive expects to receive between 2 and 4 bytes of data.

> So at this point I am questioning whether or not sendIRDongle() code is working correctly. I may have to pick up an IR sensor and turn my Arduino Uno clone into a decoder using some of the guides I've seen online to make sure I'm actually sending the correct data string.

It would definitely be interesting to try and see what it actually sends out over IR for your various send commands.

> If I can't figure this out soon, would you be willing to add this to your library with the limitation of only sending two or three bytes via IR while I continue to debug sending a fourth byte?

Sounds ok to me. From the data you have shown above though, it seems likely that it is only sending 2 - 2.5 bytes though. I guess you could run the tests I mentioned earlier and verify that fact.

Tiogaplanet, 2018-07-24:
OK, I made an IR decoder using an IR sensor I stole out of a Blu-ray in the closet.  I followed this [guide](https://www.maxphi.com/ir-remote-control-decoder-using-arduino).  I'm surprised how easy it was.

I'm also surprised by the results I received. Everything is hex below.
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
adamgreen, 2018-07-25:
That does look like it is sending a full 32-bits of data for the battle mode stuff.

adamgreen, 2018-07-25:
```48484848494849484848484849484948Found```
> I'm not sure where "Found" is coming from unless it's a buffer overrun.

Looking at the latest commit, it looks like you purposely dump the buffer twice in this scenario so that part of the dump looks ok but I don't see where the "Found" would be coming from either. If you run it multiple times, does it reproduce this output? Maybe add a println() after each of the buffer dumps to see if "Found" comes from dumping the buffer somehow or if it is output somewhere else.

adamgreen, 2018-07-25:
I just finished doing yet another code review and I don't see anything obviously wrong in the code which could cause dropped data. It definitely seems like the MiP is sending you the wrong data over the UART. I also don't see where that "Found" text is coming from. If that still repros for you and its not something in your test code somewhere, I would be worried that there is stack corruption leading to the execution of some arbitrary code upon return from a function where the return address has been corrupted.

Tiogaplanet, 2018-07-25:
It's amateur hour over here.  I wasn't intentionally dumping the buffer twice and I had line breaks in the wrong place between mip.cpp and ReceiveIRDongleCode.ino.

I just made another minor commit so you can see where I was going astray but I don't think it impacts the bug we're seeing.

Output with line breaks fixed:

```
ReceiveIRDongleCode.ino - Receive up to four bytes from another MiP using IR.
Looking for data.
0 data numbers.
Looking for data.
4848484849484948
Found 4 data numbers.
0 byte data: 0
1 byte data: 0
2 byte data: 10
3 byte data: 10
Looking for data.
4848484849484948
Found 4 data numbers.
0 byte data: 0
1 byte data: 0
2 byte data: 10
3 byte data: 10
Looking for data.
4848484849484948
Found 4 data numbers.
0 byte data: 0
1 byte data: 0
2 byte data: 10
3 byte data: 10
```

Tiogaplanet, 2018-07-25:
Should we just agree to send two IR bytes? If so, I'll start bundling this up for a PR to you.

I'd be willing to open another issue with @WowWeeLabs to report the bug.  It may not get fixed but at least it will be documented.

adamgreen, 2018-07-25:
> Should we just agree to send two IR bytes? If so, I'll start bundling this up for a PR to you.

Can you first try sending the 2 following payloads and confirm my suspicions that 3 bytes aren't reliable either?

Length (bits) | Data Sent | Data I Expect You to Receive
-|-|-
32 | 0xFF, 0xFF, 0xFF, 0xFF | 0x00, 0x0F, 0xFF, 0xFF
24 | 0xFF, 0xFF, 0xFF | 0x0F, 0xFF, 0xFF

Tiogaplanet, 2018-07-25:
Sending 0xFF, 0xFF, 0xFF, 0xFF, 4 valid actually seemed to work.

```
ReceiveIRDongleCode.ino - Receive up to four bytes from another MiP using IR.
Looking for data.
0 data numbers.
Looking for data.
0 data numbers.
Looking for data.
7070707070707070
Found 4 data numbers.
0 byte data: FF
1 byte data: FF
2 byte data: FF
3 byte data: FF
Looking for data.
7070707070707070
Found 4 data numbers.
0 byte data: FF
1 byte data: FF
2 byte data: FF
3 byte data: FF
```

But sending 0xFF, 0xFF, 0xFF, 0x00, 3 valid produces this incorrect output:
```
ReceiveIRDongleCode.ino - Receive up to four bytes from another
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

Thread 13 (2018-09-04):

Can't switch MiP into app mode on newer MiP robots

adamgreen, 2018-09-04:
I just tried installing one of my MiP ProMini boards on a recently purchased MiP and it fails to connect to the MiP as @Tiogaplanet describes in https://github.com/WowWeeLabs/MiP-BLE-Protocol/issues/20.

I have entered this issue to track my investigation into this issue from my end to see if it is caused by a hardware/software issue that I introduced or can work around.

My hardware version shows up as the following in the official iOS application:
```d060217 v1 bV0.6```

adamgreen, 2018-09-04:
Like @Tiogaplanet, I saw that not much happened at all until the first byte was changed from 0xFF to 0x00.

I attached a logic analyzer to watch the data sent back and forth between the MiP and ProMini-Pack. The logic analyzer output showed something very interesting after the 0x00 was sent instead of 0xFF. Once this change was made I saw that the MiP was responding with the following text, ```"FF01"```, at a rate of 9600 bps instead of the expected 115200.

I changed the bit rate in my Arduino library from 115200 bps to 9600 bps and then the sample started working as expected. I will spend time experimenting with solutions that might be able to auto detect this newer hardware and change the baud rate as necessary.

adamgreen, 2018-09-04:
@Tiogaplanet I suspect if you switch the baud rate at [this line](https://github.com/adamgreen/MiP_ProMini-Pack/blob/master/Arduino/MiP_ProMini_Pack_Library/src/mip.cpp#L54) to 9600, you can probably install your original Sparkfun board in the newer MiP that you have and it will work. Just note that the communications back to the PC will also be at 9600 baud so you will have to change the rate in the Arduino serial monitor as well.

This isn't a long term fix for me but I just think it interesting that the original Sparkfun board might work  on these newer bots where you hit the problem.

Tiogaplanet, 2018-09-04:
@adamgreen, good thing I still have it!  Thanks for the reminder.

Just received two more MiP's as dedicated platforms for your boards.  Will test your solution with either the original SparkFun board or an ESP8266 on the MiP I was using when I discovered the problem

adamgreen, 2018-09-05:
Fixed with commit 90f350b511f444b093d5459f8597a727d6d981a8

The library now attempts to connect with the MiP at 115200 baud and if that fails, it falls back to 9600 baud instead. It always communicates with the PC at 115200 baud.

Closed 2018-09-05.

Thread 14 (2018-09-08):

Interleave 115200 and 9600 baud init attempts

adamgreen, 2018-09-08:
Feedback from @Tiogaplanet on commit 90f350b:

> How about keeping it at five tries of 115200 and with each failure, try 9600 also?

Opening this issue to track that possibility.

adamgreen, 2018-09-22:
Fixed with commit 452b172

Closed 2018-09-22.

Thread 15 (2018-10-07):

Verifying the write to head LEDs consumes serial use

Tiogaplanet, 2018-10-07:
More of a question/suggestion than actual issue.  For animating the eyes, the verification that the write was successful uses the serial line unnecessarily, IMO.  Any appetite or suggestions for disabling the check?  Maybe disabling the checks or making two new members called:

```
void writeHeadLEDs(MiPHeadLED led1, MiPHeadLED led2, MiPHeadLED led3, MiPHeadLED led4, boolean doCheck);
void writeHeadLEDs(const MiPHeadLEDs& headLEDs, boolean doCheck);
```

For example, I am doing writes of random on/off values to each of the four eye LEDs every 500ms to indicate rain.  I don't need to verify that every random write was successful.

adamgreen, 2018-10-08:
I like the idea of adding new methods which skip the verification process for setting LEDs since as you mention there might be times when the user doesn't care if they make it through since they will set them again soon anyway. I would prefer to keep the default as it is where if you ask the library to change the LED setting, it does its best to make sure that the LED is switched to the requested state. This is more consistent with the rest of the library and hides the ugliness of error detection and recovery from the Arduino end user.

My current thought on the names of the new functions would be something like:
```c++
void unverifiedWriteHeadLEDs();
void unverifiedWriteChestLED();
```
I thought about other prefixes like _attempt_, _unsafe_, _lossy_, _unchecked_, etc. but I think _unverified_ works best. What do you think?

Tiogaplanet, 2018-10-08:
I like the use of `unverified` as a descriptor.

Next question for you, since the library has three declarations for `writeChestLED()` and two for `writeHeadLEDs()` should there be an unverified form of each one?  I am thinking not because a user may not be doing quick writes in succession when using the onTime and offTime variables.  So, I think there should be just

```
void unverifiedWriteChestLED(uint8_t red, uint8_t green, uint8_t blue);
void unverifiedWriteHeadLEDs(MiPHeadLED led1, MiPHeadLED led2, MiPHeadLED led3, MiPHeadLED led4);
void unverifiedWriteHeadLEDs(const MiPHeadLEDs& headLEDs);
```

Agree, disagree?

adamgreen, 2018-10-08:
I am inclined to do it for all of them. I can think of some scenarios where a developer might want to update the LED settings, including on/off times, at regular intervals. One example is if a distance sensor (such as ultrasonic) was connected to the MiP ProMini and they wanted to set the blink rate based on the latest ultrasonic reading. If one of those LED updates doesn't make it through, it wouldn't be the end of the world.

adamgreen, 2018-10-09:
Fixed with commit 065181cd229cabad0b67e8999c228b052c2bd145

Closed 2018-10-09.

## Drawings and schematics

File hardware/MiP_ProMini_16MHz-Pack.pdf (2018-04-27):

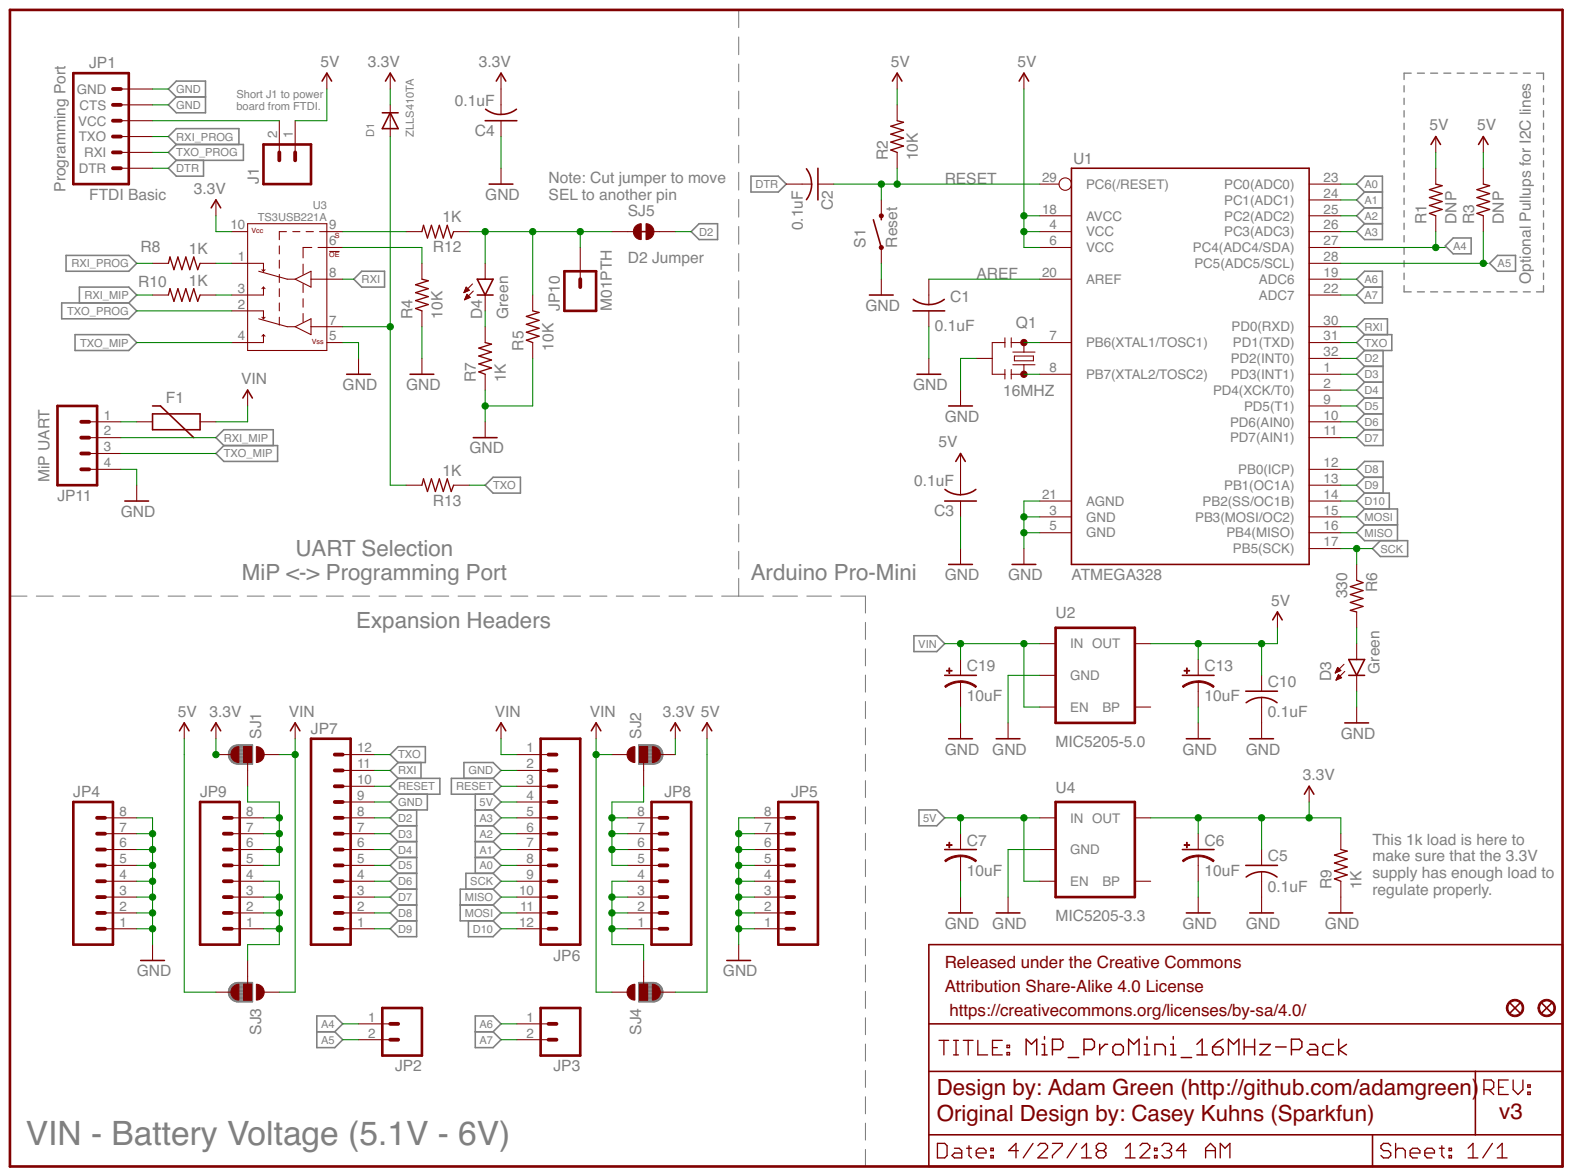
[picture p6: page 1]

Short J1 to power board from FTDI.

Optional Pullups for I2C lines

Note: Cut jumper to move SEL to another pin

This 1k load is here to make sure that the 3.3V

supply has enough load to
regulate properly.

Released under the Creative Commons Attribution Share-Alike 4.0 License

https://creativecommons.org/licenses/by-sa/4.0/

Adam Green (http://github.com/adamgreen)

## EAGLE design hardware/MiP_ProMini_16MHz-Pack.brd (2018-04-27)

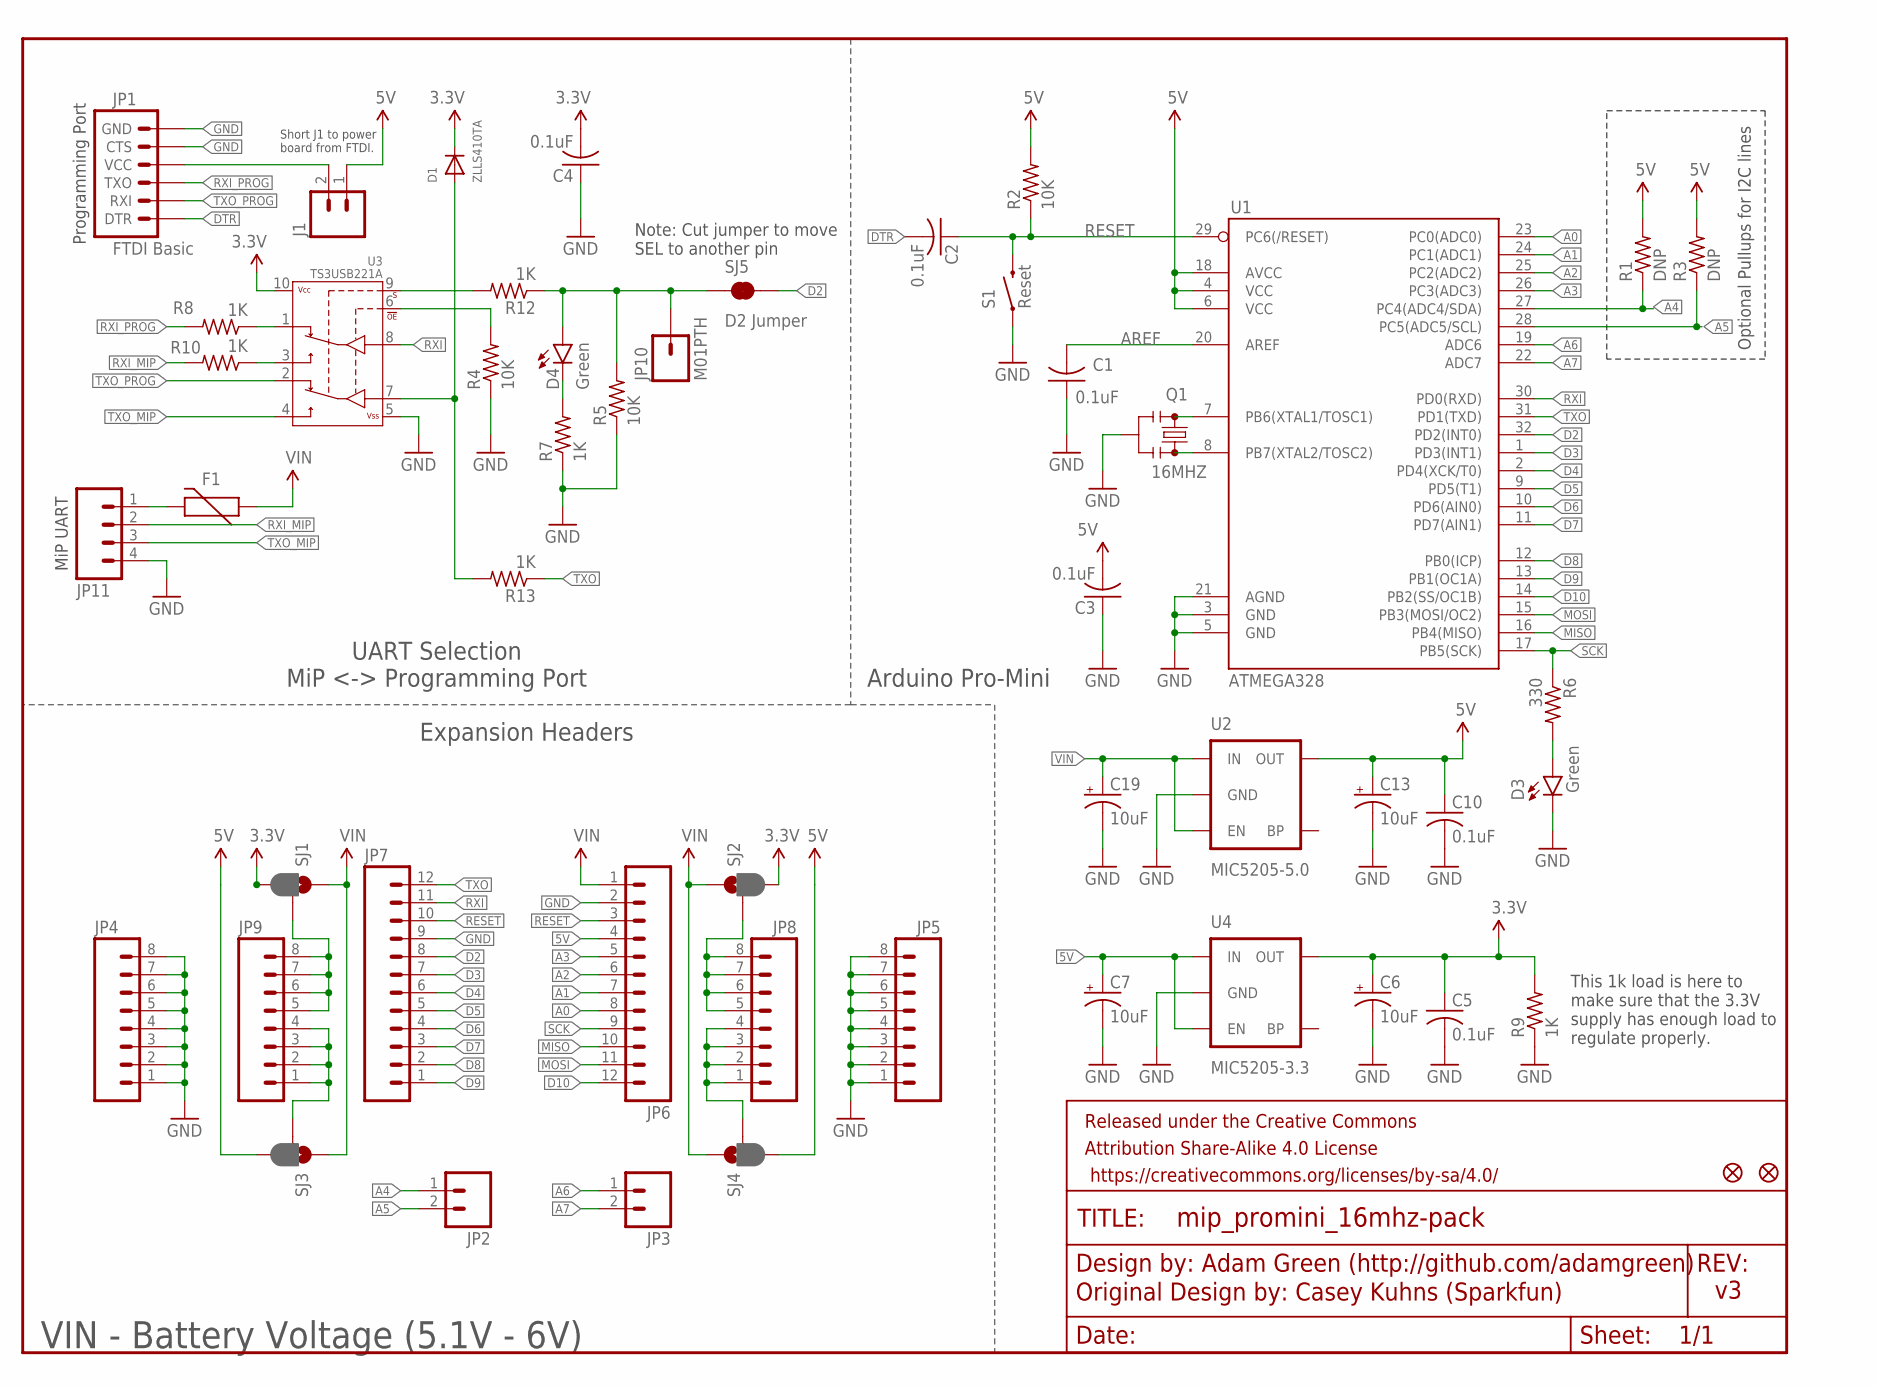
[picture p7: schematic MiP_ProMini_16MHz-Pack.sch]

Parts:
C1, C2, C3, C4, C5, C10: 0.1uF; C0805
C6, C7, C13, C19: 10uF; EIA3216
D1: ZLLS410TA; SOD-323F
D3, D4: Green; LED-0603
F1: PTCCUSTOM; PTC-1206-CUSTOM
FID1, FID2: FIDUCIAL1X2; FIDUCIAL-1X2
FRAME1: FRAME-LETTER; CREATIVE_COMMONS
J1: M02PTH; 1X02
JP1: FTDI Basic; 1X06
JP2, JP3: M02PTH; 1X02
JP4, JP5, JP8, JP9: M081X08; 1X08
JP6, JP7: M12PTH; 1X12
JP10: M01PTH; 1X01
JP11: M04JST; 1X04-1.5MM_JST
Q1: 16MHZ; RESONATOR-SMD-CUSTOM
R1, R3: DNP; R0805
R2, R4, R5: 10K; R0805
R6: 330; R0805
R7, R8, R9, R10, R12, R13: 1K; R0805
S1: Reset; TACTILE-SWITCH-SMD-CKN9112CT-ND
SJ1, SJ2, SJ3, SJ4: JUMPER-PAD-3-2OF3_NC_BY_PASTE; PAD-JUMPER-3-2OF3_NC_BY_PASTE_YES_SILK_FULL_BOX
SJ5: D2 Jumper; PAD-JUMPER-2-NC_BY_TRACE_YES_SILK
U1: ATMEGA328; TQFP32-08
U2: MIC5205-5.0; SOT23-5
U3: TS3USB221A; QFN-10-RSE-CUSTOM
U4: MIC5205-3.3; SOT23-5

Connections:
3.3V: C4.2, C5.1, C6.A (+), D1.C, R9.2, SJ1.3, SJ2.3, U3.10 (VCC), U4.5 (OUT)
5V: C3.2, C7.A (+), C10.1, C13.A (+), J1.1, JP6.4, R1.2, R2.2, R3.2, SJ3.3, SJ4.3, U1.4 (VCC), U1.6 (VCC), U1.18 (AVCC), U2.5 (OUT), U4.1 (IN), U4.3 (EN)
A0: JP6.8, U1.23 (PC0(ADC0))
A1: JP6.7, U1.24 (PC1(ADC1))
A2: JP6.6, U1.25 (PC2(ADC2))
A3: JP6.5, U1.26 (PC3(ADC3))
A4: JP2.1, R1.1, U1.27 (PC4(ADC4/SDA))
A5: JP2.2, R3.1, U1.28 (PC5(ADC5/SCL))
A6: JP3.1, U1.19 (ADC6)
A7: JP3.2, U1.22 (ADC7)
AREF: C1.2, U1.20 (AREF)
D2: JP7.8, SJ5.2, U1.32 (PD2(INT0))
D3: JP7.7, U1.1 (PD3(INT1))
D4: JP7.6, U1.2 (PD4(XCK/T0))
D5: JP7.5, U1.9 (PD5(T1))
D6: JP7.4, U1.10 (PD6(AIN0))
D7: JP7.3, U1.11 (PD7(AIN1))
D8: JP7.2, U1.12 (PB0(ICP))
D9: JP7.1, U1.13 (PB1(OC1A))
D10: JP6.12, U1.14 (PB2(SS/OC1B))
DTR: C2.2, JP1.1 (DTR)
GND: C1.1, C3.1, C4.1, C5.2, C6.C (-), C7.C (-), C10.2, C13.C (-), C19.C (-), D3.C, JP1.5 (CTS), JP1.6 (GND), JP4.1, JP4.2, JP4.3, JP4.4, JP4.5, JP4.6, JP4.7, JP4.8, JP5.1, JP5.2, JP5.3, JP5.4, JP5.5, JP5.6, JP5.7, JP5.8, JP6.2, JP7.9, JP11.4, Q1.2, R4.1, R5.1, R7.1, R9.1, S1.1, U1.3 (GND), U1.5 (GND), U1.21 (AGND), U2.2 (GND), U3.5 (VSS), U4.2 (GND)
MISO: JP6.10, U1.16 (PB4(MISO))
MOSI: JP6.11, U1.15 (PB3(MOSI/OC2))
unnamed: Q1.3, U1.8 (PB7(XTAL2/TOSC2))
unnamed: JP9.5, JP9.6, JP9.7, JP9.8, SJ1.2
unnamed: JP9.1, JP9.2, JP9.3, JP9.4, SJ3.2
unnamed: Q1.1, U1.7 (PB6(XTAL1/TOSC1))
unnamed: JP8.5, JP8.6, JP8.7, JP8.8, SJ2.2
unnamed: JP8.1, JP8.2, JP8.3, JP8.4, SJ4.2
unnamed: D3.A, R6.2
unnamed: D4.C, R7.2
unnamed: R10.1, U3.3 (2D+)
unnamed: R8.1, U3.1 (1D+)
unnamed: R4.2, U3.6 (!OE)
unnamed: J1.2, JP1.4 (VCC)
unnamed: R12.2, U3.9 (S)
unnamed: F1.2, JP11.1
unnamed: D1.A, R13.2, U3.7 (D-)
RESET: C2.1, JP6.3, JP7.10, R2.1, S1.3 (2), U1.29 (PC6(/RESET))
RXI: JP7.11, U1.30 (PD0(RXD)), U3.8 (D+)
RXI_MIP: JP11.2, R10.2
RXI_PROG: JP1.3 (TXO), R8.2
SCK: JP6.9, R6.1, U1.17 (PB5(SCK))
SELECT: D4.A, JP10.1, R5.2, R12.1, SJ5.1
TXO: JP7.12, R13.1, U1.31 (PD1(TXD))
TXO_MIP: JP11.3, U3.4 (2D-)
TXO_PROG: JP1.2 (RXI), U3.2 (1D-)
VIN: C19.A (+), F1.1, JP6.1, SJ1.1, SJ2.1, SJ3.1, SJ4.1, U2.1 (IN), U2.3 (EN)

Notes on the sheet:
Optional Pullups for I2C lines
Adam Green (http://github.com/adamgreen)
Note: Cut jumper to move SEL to another pin
MiP UART
Programming Port
UART Selection MiP <-> Programming Port
Expansion Headers
Arduino Pro-Mini
VIN - Battery Voltage (5.1V - 6V)
Original Design by: Casey Kuhns (Sparkfun)
Short J1 to power board from FTDI.
This 1k load is here to make sure that the 3.3V supply has enough load to regulate properly.

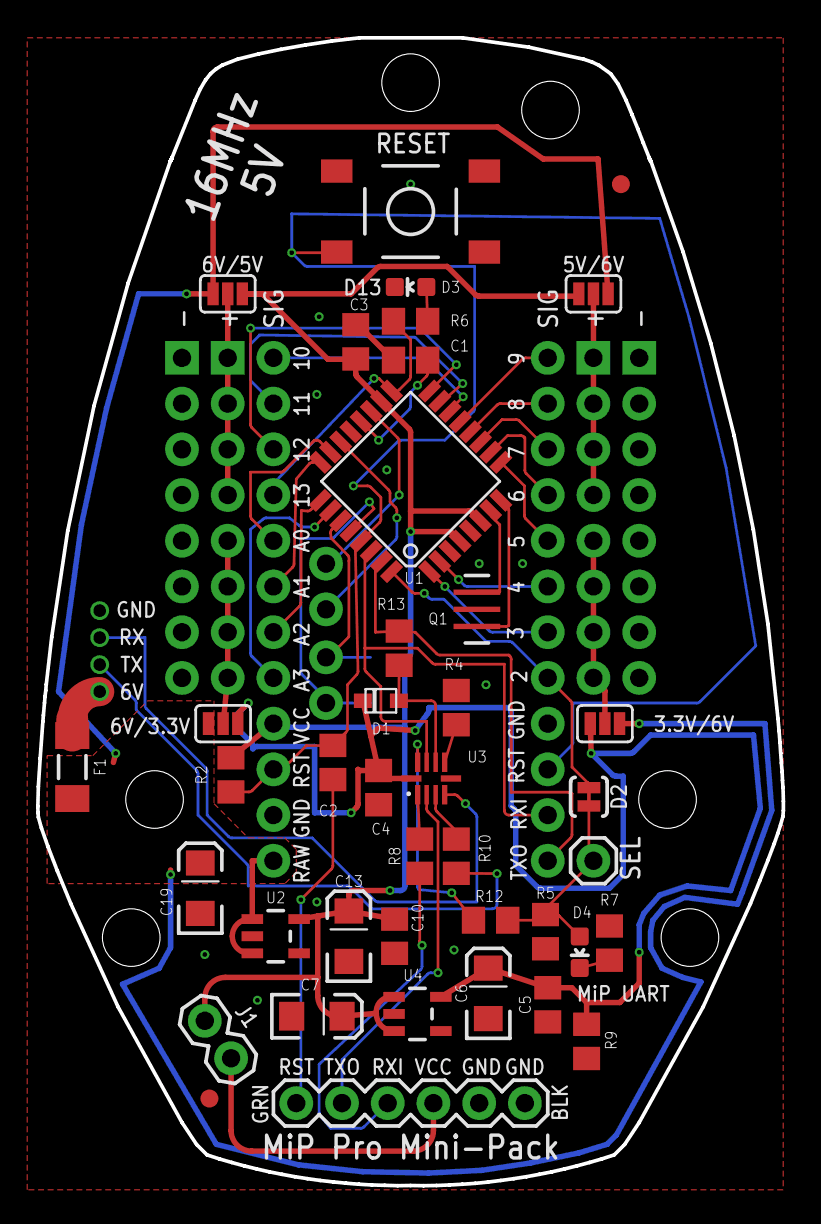
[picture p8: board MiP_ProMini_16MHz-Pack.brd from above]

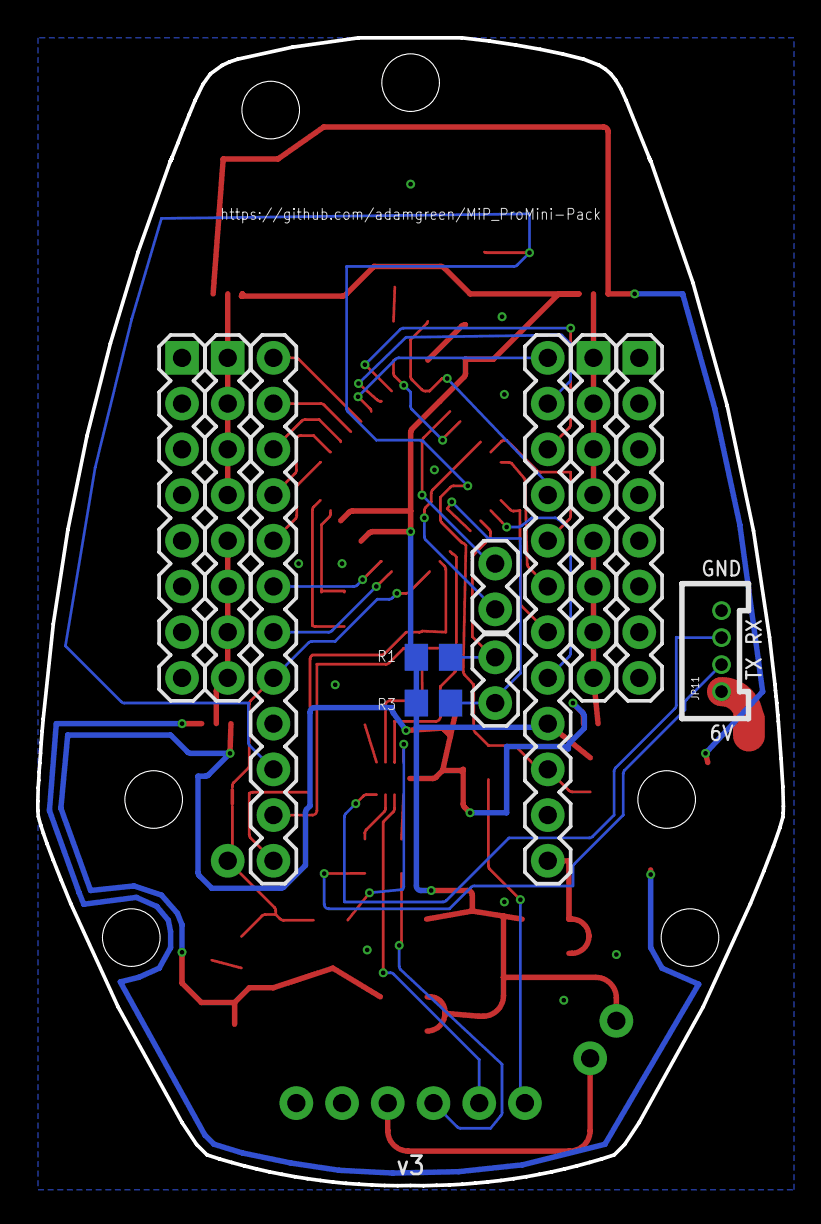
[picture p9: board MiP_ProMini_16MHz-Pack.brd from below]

Board: 2 copper layers, 41.4 x 63.8 mm, 52 parts (11 on the bottom side), 49 nets.

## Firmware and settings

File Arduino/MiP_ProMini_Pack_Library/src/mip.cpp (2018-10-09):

/* Copyright (C) 2018  Adam Green (https://github.com/adamgreen)

   Licensed under the Apache License, Version 2.0 (the "License");
   you may not use this file except in compliance with the License.
   You may obtain a copy of the License at

       http://www.apache.org/licenses/LICENSE-2.0

   Unless required by applicable law or agreed to in writing, software
   distributed under the License is distributed on an "AS IS" BASIS,
   WITHOUT WARRANTIES OR CONDITIONS OF ANY KIND, either express or implied.
   See the License for the specific language governing permissions and
   limitations under the License.
*/
/* Implementation of MiP C API. */
#include "mip.h"


// Make sure that the MiP module itself always uses the actual Serial object and not the redirection to MiPStream.
#undef Serial


// Number of times that begin() method should try to initialize the MiP.
#define MIP_MAX_BEGIN_RETRIES 5

// Number of milliseconds to wait between retries in begin().
#define MIP_BEGIN_RETRY_WAIT 500

// Number of times to retry methods other than begin().
#define MIP_MAX_RETRIES 2

// Number of milliseconds to wait between retries in methods other than begin().
#define MIP_RETRY_WAIT 50

// Should timeout if expected response doesn't arrive back in this amount of time (in milliseconds).
#define MIP_RESPONSE_TIMEOUT 100

// Delay between requests sent to MiP (in milliseconds). If the user attempts to send requests to the MiP faster than
// this, the library will busy wait and only continue with the request after this amount of time has passed. The MiP
// will sometimes ignore requests sent faster than this.
#define MIP_REQUEST_DELAY 8

// Delay between continuousDrive requests sent to MiP (in milliseconds). continuousDrive() will just ignore faster
// requests.
#define MIP_CONTINUOUS_DRIVE_DELAY 50

// EEPROM base address.  When reading or writing to EEPROM the user will pass an offset that is added to this base address.
#define MIP_BASE_EEPROM_ADDRESS 0x20

// Last addressable address in EEPROM.
#define MIP_LAST_EEPROM_ADDRESS 0x2F

// Baud rate to use for MiP/PC communications.
#define MIP_BAUD_RATE 115200

// Slower baud rate used by newer MiP robots.
#define MIP_SLOWER_BAUD_RATE 9600

// MiP Protocol Commands.
// These command codes are placed in the first byte of requests sent to the MiP and responses sent back from the MiP.
// See https://github.com/WowWeeLabs/MiP-BLE-Protocol/blob/master/MiP-Protocol.md for more information.
#define MIP_CMD_RECEIVE_IR_DONGLE_CODE  0x03
#define MIP_CMD_GET_DETECTED_MIP        0x04
#define MIP_CMD_PLAY_SOUND              0x06
#define MIP_CMD_SET_POSITION            0x08
#define MIP_CMD_GET_GESTURE_RESPONSE    0x0A
#define MIP_CMD_SET_GESTURE_RADAR_MODE  0x0C
#define MIP_CMD_GET_RADAR_RESPONSE      0x0C
#define MIP_CMD_GET_GESTURE_RADAR_MODE  0x0D
#define MIP_CMD_SET_DETECTION_MODE      0x0E
#define MIP_CMD_SET_IR_REMOTE_CONTROL   0x10
#define MIP_CMD_GET_IR_REMOTE_CONTROL   0x11
#define MIP_CMD_SET_USER_DATA           0x12
#define MIP_CMD_GET_USER_DATA           0x13
#define MIP_CMD_GET_SOFTWARE_VERSION    0x14
#define MIP_CMD_SET_VOLUME              0x15
#define MIP_CMD_GET_VOLUME              0x16
#define MIP_CMD_GET_HARDWARE_INFO       0x19
#define MIP_CMD_SHAKE_RESPONSE          0x1A
#define MIP_CMD_CLAP_RESPONSE           0x1D
#define MIP_CMD_ENABLE_CLAP             0x1E
#define MIP_CMD_GET_CLAP_SETTINGS       0x1F
#define MIP_CMD_SET_CLAP_DELAY          0x20
#define MIP_CMD_GET_UP                  0x23
#define MIP_CMD_DISTANCE_DRIVE          0x70
#define MIP_CMD_DRIVE_FORWARD           0x71
#define MIP_CMD_DRIVE_BACKWARD          0x72
#define MIP_CMD_TURN_LEFT               0x73
#define MIP_CMD_TURN_RIGHT              0x74
#define MIP_CMD_SET_GAME_MODE           0x76
#define MIP_CMD_STOP                    0x77
#define MIP_CMD_CONTINUOUS_DRIVE        0x78
#define MIP_CMD_GET_STATUS              0x79
#define MIP_CMD_GET_WEIGHT              0x81
#define MIP_CMD_GET_GAME_MODE           0x82
#define MIP_CMD_GET_CHEST_LED           0x83
#define MIP_CMD_SET_CHEST_LED           0x84
#define MIP_CMD_READ_ODOMETER           0x85
#define MIP_CMD_RESET_ODOMETER          0x86
#define MIP_CMD_FLASH_CHEST_LED         0x89
#define MIP_CMD_SET_HEAD_LEDS           0x8A
#define MIP_CMD_GET_HEAD_LEDS           0x8B
#define MIP_CMD_SEND_IR_DONGLE_CODE     0x8C
#define MIP_CMD_SLEEP                   0xFA
#define MIP_CMD_DISCONNECT_APP          0xFE


// expectResponse parameter values for transportSendRequest() parameter.
#define MIP_EXPECT_NO_RESPONSE 0
#define MIP_EXPECT_RESPONSE    1


// IR mode definitions.
#define MIP_IR_DETECTION_MODE_DISABLE 0
#define MIP_IR_REMOTE_CONTROL_DISABLE 0
#define MIP_IR_REMOTE_CONTROL_ENABLE  1


// It is expected that the user will only instantiate a single MiP object (mostly likely a global object). This
// pointer is set from within that singleton's constructor and later used by the global MiPStream when it needs to
// call upon the MiP object to switch the UART between MiP and PC.
MiP* MiP::s_pInstance = NULL;



// Define an assert mechanism that can be used to log and halt when the user is found to be calling the API incorrectly.
#define MIP_ASSERT(EXPRESSION) if (!(EXPRESSION)) mipAssert(__LINE__);

static void mipAssert(uint32_t lineNumber)
{
    MiPStream.print(F("MiP Assert: mip.cpp:"));
        MiPStream.println(lineNumber);

    while (1)
    {
    }
}



MiP::MiP(int8_t serialSelectPin /* = MIP_UART_SELECT_PIN */)
{
    m_serialSelectPin = serialSelectPin;

    clear();

    // Track this instance in class specific global so that MiPStream can find it.
    s_pInstance = this;
}

MiP::~MiP()
{
    end();
    s_pInstance = NULL;
}

void MiP::clear()
{
    m_lastRequestTime = millis();
    m_lastContinuousDriveTime = millis();
    m_mipBaudRate = MIP_BAUD_RATE;
    m_flags = 0;
    memset(m_responseBuffer, 0, sizeof(m_responseBuffer));
    m_expectedResponseCommand = 0;
    m_expectedResponseSize = 0;
    m_lastError = MIP_ERROR_NONE;
    m_soundIndex = -1;
    m_lastRadar = MIP_RADAR_INVALID;
    m_lastStatus.clear();
    m_lastWeight = 0;
    m_clapEvents.clear();
    m_gestureEvents.clear();
    m_detectedMiPEvents.clear();
    m_irCodeEvents.clear();
    m_irId = 0x00;
}
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

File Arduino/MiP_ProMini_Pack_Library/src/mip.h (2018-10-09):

/* Copyright (C) 2018  Adam Green (https://github.com/adamgreen)

   Licensed under the Apache License, Version 2.0 (the "License");
   you may not use this file except in compliance with the License.
   You may obtain a copy of the License at

       http://www.apache.org/licenses/LICENSE-2.0

   Unless required by applicable law or agreed to in writing, software
   distributed under the License is distributed on an "AS IS" BASIS,
   WITHOUT WARRANTIES OR CONDITIONS OF ANY KIND, either express or implied.
   See the License for the specific language governing permissions and
   limitations under the License.
*/
/* This header file describes the public API that an application can use to communicate with the WowWee MiP
   self-balancing robot.
*/
#ifndef MIP_H_
#define MIP_H_

#include <Arduino.h>
#include <stdint.h>
#include <stdlib.h>
#include "queue.h"

// Default pin used by the TS3USB221A switch to connect Serial to the MiP or PC.
//   Set to HIGH, it selects the MiP.
//   Set to LOW, it selects the PC.
#define MIP_UART_SELECT_PIN 2


// Integer error codes that can be encountered by MiP API functions.
#define MIP_ERROR_NONE          0 // Success
#define MIP_ERROR_TIMEOUT       1 // Timed out waiting for response.
#define MIP_ERROR_NO_EVENT      2 // No event has arrived from MiP yet.
#define MIP_ERROR_BAD_RESPONSE  3 // Unexpected response from MiP.
#define MIP_ERROR_MAX_RETRIES   4 // Exceeded maximum number of retries to get this operation to succeed.

// Maximum length of MiP request and response buffer lengths.
#define MIP_REQUEST_MAX_LEN     (17 + 1)    // Longest request is MIP_CMD_PLAY_SOUND.
#define MIP_RESPONSE_MAX_LEN    (5 + 1)     // Longest response is MIP_CMD_REQUEST_CHEST_LED.

enum MiPGestureRadarMode
{
    MIP_GESTURE_RADAR_DISABLED = 0x00,
    MIP_GESTURE                = 0x02,
    MIP_RADAR                  = 0x04,
};

enum MiPRadar
{
    MIP_RADAR_NONE      = 0x01,
    MIP_RADAR_10CM_30CM = 0x02,
    MIP_RADAR_0CM_10CM  = 0x03,
    MIP_RADAR_INVALID   = 0xFF          // Is set to this value when there are no current radar events.
};

enum MiPGesture
{
    MIP_GESTURE_LEFT               = 0x0A,
    MIP_GESTURE_RIGHT              = 0x0B,
    MIP_GESTURE_CENTER_SWEEP_LEFT  = 0x0C,
    MIP_GESTURE_CENTER_SWEEP_RIGHT = 0x0D,
    MIP_GESTURE_CENTER_HOLD        = 0x0E,
    MIP_GESTURE_FORWARD            = 0x0F,
    MIP_GESTURE_BACKWARD           = 0x10,
    MIP_GESTURE_INVALID            = 0xFF   // Is set to this value when there are no current gesture events.
};

enum MiPHeadLED
{
    MIP_HEAD_LED_OFF        = 0,
    MIP_HEAD_LED_ON         = 1,
    MIP_HEAD_LED_BLINK_SLOW = 2,
    MIP_HEAD_LED_BLINK_FAST = 3,
};

enum MiPDriveDirection
{
    MIP_DRIVE_FORWARD  = 0x00,
    MIP_DRIVE_BACKWARD = 0x01,
};

enum MiPTurnDirection
{
    MIP_TURN_LEFT  = 0x00,
    MIP_TURN_RIGHT = 0x01
};

enum MiPFallDirection
{
    MIP_FALL_ON_BACK   = 0x00,
    MIP_FALL_FACE_DOWN = 0x01
};

enum MiPPosition
{
    MIP_POSITION_ON_BACK                = 0x00,
    MIP_POSITION_FACE_DOWN              = 0x01,
    MIP_POSITION_UPRIGHT                = 0x02,
    MIP_POSITION_PICKED_UP              = 0x03,
    MIP_POSITION_HAND_STAND             = 0x04,
    MIP_POSITION_FACE_DOWN_ON_TRAY      = 0x05,
    MIP_POSITION_ON_BACK_WITH_KICKSTAND = 0x06,
};

enum MiPGetUp
{
    MIP_GETUP_FROM_FRONT  = 0x00,
    MIP_GETUP_FROM_BACK   = 0x01,
    MIP_GETUP_FROM_EITHER = 0x02
};

enum MiPSoundIndex
{
    MIP_SOUND_ONEKHZ_500MS_8K16BIT = 1,
    MIP_SOUND_ACTION_BURPING,
    MIP_SOUND_ACTION_DRINKING,
    MIP_SOUND_ACTION_EATING,
    MIP_SOUND_ACTION_FARTING_SHORT,
    MIP_SOUND_ACTION_OUT_OF_BREATH,
    MIP_SOUND_BOXING_PUNCHCONNECT_1,
    MIP_SOUND_BOXING_PUNCHCONNECT_2,
    MIP_SOUND_BOXING_PUNCHCONNECT_3,
    MIP_SOUND_FREESTYLE_TRACKING_1,
    MIP_SOUND_MIP_1,
    MIP_SOUND_MIP_2,
    MIP_SOUND_MIP_3,
    MIP_SOUND_MIP_APP,
    MIP_SOUND_MIP_AWWW,
    MIP_SOUND_MIP_BIG_SHOT,
    MIP_SOUND_MIP_BLEH,
    MIP_SOUND_MIP_BOOM,
    MIP_SOUND_MIP_BYE,
    MIP_SOUND_MIP_CONVERSE_1,
    MIP_SOUND_MIP_CONVERSE_2,
    MIP_SOUND_MIP_DROP,
    MIP_SOUND_MIP_DUNNO,
    MIP_SOUND_MIP_FALL_OVER_1,
    MIP_SOUND_MIP_FALL_OVER_2,
    MIP_SOUND_MIP_FIGHT,
    MIP_SOUND_MIP_GAME,
    MIP_SOUND_MIP_GLOAT,
    MIP_SOUND_MIP_GO,
    MIP_SOUND_MIP_GOGOGO,
    MIP_SOUND_MIP_GRUNT_1,
    MIP_SOUND_MIP_GRUNT_2,
    MIP_SOUND_MIP_GRUNT_3,
    MIP_SOUND_MIP_HAHA_GOT_IT,
    MIP_SOUND_MIP_HI_CONFIDENT,
    MIP_SOUND_MIP_HI_NOT_SURE,
    MIP_SOUND_MIP_HI_SCARED,
    MIP_SOUND_MIP_HUH,
    MIP_SOUND_MIP_HUMMING_1,
    MIP_SOUND_MIP_HUMMING_2,
    MIP_SOUND_MIP_HURT,
    MIP_SOUND_MIP_HUUURGH,
    MIP_SOUND_MIP_IN_LOVE,
    MIP_SOUND_MIP_IT,
    MIP_SOUND_MIP_JOKE,
    MIP_SOUND_MIP_K,
    MIP_SOUND_MIP_LOOP_1,
    MIP_SOUND_MIP_LOOP_2,
    MIP_SOUND_MIP_LOW_BATTERY,
    MIP_SOUND_MIP_MIPPEE,
    MIP_SOUND_MIP_MORE,
    MIP_SOUND_MIP_MUAH_HA,
    MIP_SOUND_MIP_MUSIC,
    MIP_SOUND_MIP_OBSTACLE,
    MIP_SOUND_MIP_OHOH,
    MIP_SOUND_MIP_OH_YEAH,
    MIP_SOUND_MIP_OOPSIE,
    MIP_SOUND_MIP_OUCH_1,
    MIP_SOUND_MIP_OUCH_2,
    MIP_SOUND_MIP_PLAY,
    MIP_SOUND_MIP_PUSH,
    MIP_SOUND_MIP_RUN,
    MIP_SOUND_MIP_SHAKE,
    MIP_SOUND_MIP_SIGH,
    MIP_SOUND_MIP_SINGING,
    MIP_SOUND_MIP_SNEEZE,
    MIP_SOUND_MIP_SNORE,
    MIP_SOUND_MIP_STACK,
    MIP_SOUND_MIP_SWIPE_1,
    MIP_SOUND_MIP_SWIPE_2,
    MIP_SOUND_MIP_TRICKS,
    MIP_SOUND_MIP_TRIIICK,
    MIP_SOUND_MIP_TRUMPET,
    MIP_SOUND_MIP_WAAAAA,
    MIP_SOUND_MIP_WAKEY,
    MIP_SOUND_MIP_WHEEE,
    MIP_SOUND_MIP_WHISTLING,
    MIP_SOUND_MIP_WHOAH,
    MIP_SOUND_MIP_WOO,
    MIP_SOUND_MIP_YEAH,
    MIP_SOUND_MIP_YEEESSS,
    MIP_SOUND_MIP_YO,
    MIP_SOUND_MIP_YUMMY,
    MIP_SOUND_MOOD_ACTIVATED,
    MIP_SOUND_MOOD_ANGRY,
    MIP_SOUND_MOOD_ANXIOUS,
    MIP_SOUND_MOOD_BORING,
    MIP_SOUND_MOOD_CRANKY,
    MIP_SOUND_MOOD_ENERGETIC,
    MIP_SOUND_MOOD_EXCITED,
    MIP_SOUND_MOOD_GIDDY,
    MIP_SOUND_MOOD_GRUMPY,
    MIP_SOUND_MOOD_HAPPY,
    MIP_SOUND_MOOD_IDEA,
    MIP_SOUND_MOOD_IMPATIENT,
    MIP_SOUND_MOOD_NICE,
    MIP_SOUND_MOOD_SAD,
    MIP_SOUND_MOOD_SHORT,
    MIP_SOUND_MOOD_SLEEPY,
    MIP_SOUND_MOOD_TIRED,
    MIP_SOUND_SOUND_BOOST,
    MIP_SOUND_SOUND_CAGE,
    MIP_SOUND_SOUND_GUNS,
    MIP_SOUND_SOUND_ZINGS,
    MIP_SOUND_SHORT_MUTE_FOR_STOP,
    MIP_SOUND_FREESTYLE_TRACKING_2,
    MIP_SOUND_VOLUME_OFF = 0xF7,
    MIP_SOUND_VOLUME_1   = 0xF8,
    MIP_SOUND_VOLUME_2   = 0xF9,
    MIP_SOUND_VOLUME_3   = 0xFA,
    MIP_SOUND_VOLUME_4   = 0xFB,
    MIP_SOUND_VOLUME_5   = 0xFC,
    MIP_SOUND_VOLUME_6   = 0xFD,
    MIP_SOUND_VOLUME_7   = 0xFE
};

enum MiPVolume
{
    MIP_VOLUME_OFF = 0,
    MIP_VOLUME_1   = 1,
    MIP_VOLUME_2   = 2,
    MIP_VOLUME_3   = 3,
    MIP_VOLUME_4   = 4,
    MIP_VOLUME_5   = 5,
    MIP_VOLUME_6   = 6,
    MIP_VOLUME_7   = 7,
    MIP_VOLUME_DEFAULT = 0xFF
};

enum MiPClapEnabled
{
    MIP_CLAP_DISABLED = 0x00,
    MIP_CLAP_ENABLED  = 0x01,
};
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

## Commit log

2018-02-26 Rename Eagle files
    Remove Sparkfun from filenames since I don't want to infringe on their
    trademark for my variation of the board.
    [MiP_ProMini_16MHz-Pack.brd, MiP_ProMini_16MHz-Pack.sch]
2018-02-26 Update schematic to 16MHz / 5V
    The ATMEGA328 can't reliably receive data from the MiP at 115200 bps
    when running at 8MHz. This commit bumps the clock rate up to 16MHz and
    bumps the voltage up to 5V so that the AVR can reliably run at this
    higher rate.
    Other changes to the schematic include:
    * By default the VCC pin of the FTDI header is no longer connected to
    anything. This was done so that the user doesn't risk powering the
    board from both the MiP batteries and the FTDI adapter at the same
    time. It also means that the user doesn't need to worry about whether
    their FTDI adapter is configured to place 5V or 3.3V on this pin. If
    the user wants to power the board from a 5V FTDI cable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
    [MiP_ProMini_16MHz-Pack.brd, MiP_ProMini_16MHz-Pack.sch]
2018-03-01 Add 3.3V to headers for v2
    Revision 2 of the schematic now allows the lower portion of the
    vertical power buses to be selected between 3.3V and 6V while the upper
    portion can be selected between 5V and 6V. Previously only the
    regulated 5V and unregulated 6V were available for prototyping but it
    makes sense to expose the regulated 3.3V as well incase the user wants
    to use 3.3V peripherals.
    [MiP_ProMini_16MHz-Pack.brd, MiP_ProMini_16MHz-Pack.sch]
2018-03-10 Initial layout complete
    No more air wires to route and passes OSHPark DRC.
    Important notes:
    * I had to move the A6/A7 1x2 jumper block to move the AVR up higher on
    the board. This was done to make more room for larger passives and an
    extra voltage regulator lower on the board.
    * I ended up removing the AVR-ISP port since I couldn't fit it on the
    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
    [MiP_ProMini_16MHz-Pack.brd, MiP_ProMini_16MHz-Pack.sch]
2018-03-10 Update README
    Added notes about what was changed on PCB to make soldering easier and
    removed the AVRISP header item since it wasn't convenient to place and
    route.
2018-03-10 Use consistent case for 1K resistor value
    I had used 1k in some places and 1K in others so that 2 different items
    showed up in BOM.
    [MiP_ProMini_16MHz-Pack.brd, MiP_ProMini_16MHz-Pack.sch]
2018-03-10 Tidy up silkscreen names
    I moved some of the part names around so that they would be a bit
    easier to read (small size will still make them tricky to read). I also
    smashed some parts and removed names/values all together since they
    just made things more cluttered and confusing.
    [MiP_ProMini_16MHz-Pack.brd]
2018-03-10 Adding PCB images from OSHPark
    These are OSHPark generated images of the top/bottom sides of the PCB
    that I sent off to have made today.
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2018-03-10 Add images to README
    README now shows schematic and PCB images towards the bottom of the
    page.
2018-03-10 Version 3 - Route all power headers on top layer
    Previously I had the upper right power rail in the user prototype area
    routed on the bottom layer whereas the rest were routed on the bottom.
    This commit makes them all the same and makes it easier for the user
    to see which pads are connected to what just by looking at the traces
    through the top soldermask.
    [MiP_ProMini_16MHz-Pack.brd]
2018-03-10 Update schematic version to 3
    I should have done this earlier when I removed the AVR-ISP header,
    etc.
    [MiP_ProMini_16MHz-Pack.sch]
2018-03-11 Added tRestrict to 16MHz resonator part
    This keeps the ground plane and wires out of the tStop area that was
    already defined for the resonator.
    [MiP_ProMini_16MHz-Pack.brd, MiP_ProMini_16MHz-Pack.sch]
2018-04-16 Add missing values to schematic
    [MiP_ProMini_16MHz-Pack.sch]
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2018-04-19 Initial port of MiP-Capi to Arduino
    This commit is just a placeholder. It contains a rough port of my
    existing C API to the Arduino. All of the existing samples work with
    the revised version of the MiP ProMini Pack in this repository. There
    will be several follow-up commits to make it a C++ class, more robust,
    and more closely match the style of other Arduino libraries.
2018-04-19 Update PRINT & PRINTLN macros
    No longer hardcodes the UART select pin and instead uses static methods
    on the MiP class to switch the UART between the MiP and PC.
    [mip.cpp, mip.h]
2018-04-20 Pull transport layer into MiP class
    This gets rid of mip-arduino.cpp and mip-transport.h as all the
    required code from these sources has been pulled into mip.h and mip.cpp
    Other updates include:
    * Default releaseSerialToPc in the constructor to false. This allows
    MiP out of band notifications to be captured more reliably but does
    mean that users of the MiP object must switch Serial back to the PC
    before attempting to send diagnostic output. The PRINT() and
    PRINTLN() macroes will do this for the user automatically. This has
    been documented in all of the examples now.
    * The examples have been updated to check for connection errors being
    returned from begin() and no longer continue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
    [Clap.ino, ContinuousDrive.ino, DistanceDrive.ino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]
2018-04-20 Refactor out of band notification handling
    Previously out of band notifications would be placed in a circular
    queue when they were encountered in the serial data stream received
    from the MiP. They would only be pulled from this circular queue and
    parsed when the user asked for a notification. The code now parses
    the out of band notifications as soon as they are encountered in
    input serial data stream. The circular queue is no longer required.
    NOTE: I did remove the rawReceiveNotification() method which used to
    manually pull notifications from the circular queue since the
    queue no longer exists and they are parsed as soon as they are
    encountered.
    [mip.cpp, mip.h]
2018-04-20 Handle MIP_REQUEST_DELAY differently
    Previously transportSendRequest() would just call delay() for this
    number of milliseconds to make sure that no two requests could be
    issued in less time than this. Now it just delays at the top of the
    function if this many milliseconds haven't already elapsed since it
    was last called. This lets the caller use the CPU to do something
    else between calls if they want.
    [mip.cpp, mip.h]
2018-04-20 API cleanup
    API updates include:
    * Switch most of the structs to classes with constructors.
    * Use references for passing output objects into APIs instead of
    pointers.
    * Notification related functions will now fail with a
    MIP_NO_NOTIFICATIONS error if releaseSerialToPC isn't set to false in
    the MiP constructor. I updated all of the notification related
    examples to do this.
    [Clap.ino, ContinuousDrive.ino, DistanceDrive.ino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]
2018-04-20 Clear outputs
    Clear output parameters within APIs so that they don't contain random
    values if the function should error out.
    [mip.cpp]
2018-04-22 Fix compiler warnings
    I bumped the warning level up to "All" in the Arduino IDE and fixed
    the resulting warnings.
    Changes include:
    * Adding a MIP_PRINT_ERRORS() macro to mip.h which checks a result code
    returned from a MiP method and prints out an error message if the
    result isn't MIP_ERROR_NONE. Actually reading the result code this
    way eliminates "variable set but not used" warnings.
    * Add INVALID values for many of the enumerations, to which object
    construtors will use for an initial value. I also added a clear()
    method to these same classes to perform the initialization
    explicitly. Even after construction.
    * In the begin() method, I moved the delay(30) up to after the rawSen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
    [Clap.ino, ContinuousDrive.ino, DistanceDrive.ino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]
2018-04-24 Make the library API more Arduino friendly
    This commit is mostly about simplifying the API model and bringing it
    closer to other Arduino APIs.
    The changes in this commit include:
    * When mip.h is included in a user's program, it now substitutes all of
    their usage of Serial with MiPStream. For example,
    "Serial.println("Sample")" will actually become
    "MiPStream.println("Sample")". This allows MiPStream to intercept the
    output request and change the AVR's hardware serial port to the PC
    instead of the MiP. This should allow the user to send debug output
    to the PC like they are accustomed and it will automatically end up
    going to the correct place without any extra work on their beh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
    [ChestLED.ino, Clap.ino, ContinuousDrive.ino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]
2018-04-26 Adding Arduino API documentation
    This is my first attempt at documenting the library I created for
    Arduino.
2018-04-26 Minor updates to examples
    Most of the examples were just updated to make sure that the last
    line of code ended with a newline. The ChestLED example had its print
    output updated to reflect the new name of this example.
2018-04-27 Add a 1k load across 3.3V supply
    Without this load, the 3.3V supply was closer to 4.4V. The datasheet
    for the regulator indicates that it doesn't have a minimum load to
    maintain regulation but it also indicates that the output capacitance
    can be closer to 0.5uF when the output current is only 1mA. If a
    person was using the 3.3V supply for something else that was putting
    a >= 1mA load on it then they could omit this resistor. Lowering the
    output capacitance (which was copied from the original Sparkfun design)
    might also correct the problem.
    [MiP_ProMini_16MHz-Pack.brd, MiP_ProMini_16MHz-Pack.sch]
2018-04-27 Update content for version 3
    * I moved the name marking for R9 so that it wasn't so cramped.
    * I uploaded the OSH Park PCB renderings of version 3.
    * I uploaded the latest schematic as well.
    [MiP_ProMini_16MHz-Pack.brd]
2018-04-27 Update main README
    * Switch to renderings of version 3 for the schematics and PCBs.
    * Highlight the fact that a new Arduino library was written as well
2018-05-23 Reordered BOM list
    The reordered the list to match the order that I solder them.
2018-07-02 Fix issue #3 - Refactor sound playing API
    * Added playSound() function which makes it much easier for a user to
    start the MiP immediately playing a single sound. No need to use the
    sound list to queue up sounds and then signal the MiP to start
    playing the queue.
    * Updated addEntryToSoundList() to accept an optional volume parameter.
    This makes it easier for the user to set the volume to be used for
    particular sound entries in the queue. They no longer need to worry
    about the special usage of the MIP_SOUND_VOLUME_* sound entries.
    * Made the delay parameter for addEntryToSoundList() optional.
    * Made the repeatCount parameter for playSoundList() optional.
    [PlaySound.ino, mip.cpp, mip.h]
2018-07-03 Fixes issue #5 - Switch end() to just disconnect and add sleep()
    Updated the existing end() function to use the new disconnect
    functionality and exposes the old behavior via a new sleep() method.
    [Sleep.ino, mip.cpp, mip.h]
2018-07-04 Stop before issuing actual set/get game mode commands
    I updated rawSetGameMode() and rawGetGameMode() to call stop() before
    running the actual set/get game mode command. This allows the MiP to
    accept those commands more reliably when it is actively moving around
    as part of the current game mode.
    The rawGetGameMode() command will reinstate the previously stopped game
    mode once the mode has been successfully received from the MiP.
    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
2018-07-04 Remove extraneous begin() from examples
    I had done this before for most of the examples but somehow missed
    SoftwareHardwareVersion and ended up using it as the template for the
    newer Sleep example.
    [Sleep.ino, SoftwareHardwareVersion.ino]
2018-07-04 Incremental improvement to reading/writing EEPROM
    I found a couple obvious bugs in creating the mip command array to send
    to the mip. Added some documentaton. Will link example in readme
    later.
    [ReadWriteEeprom.ino]
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2018-07-22 Nearly complete with implementing IR stuff
    The implementation of receiving IR dongle code is buggy. Everything
    else seems to work.
    [EnableMiPDetectionMode.ino, mip.cpp, mip.h]
2018-07-25 Another review commit
    I was dumping the buffer twice, line breaks in the wrong places, amateur
    hour over here.
    [mip.cpp]
2018-07-25 Tidying up before PR.
    Won't do PR tonight but cleaning up code in preparation for PR.
    [EnableMiPDetectionMode.ino, SendIRDongleCode.ino, mip.cpp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]
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2018-09-02 README updates
    * Add links section.
    * Added a note that the most important goal of this project is to fix
    the serial communication issue in the Sparkfun original.
    * Reordered some BOM items to match the order that I now solder them.
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2018-09-04 This makes it easier to try out 9600 bps on newer MiP robots and test out a workaround for issue #13 while I investigate a better long term remedy.
    [mip.cpp]
2018-09-05 Auto switch to 9600 baud for newer MiP robots
    The MiP::begin() call will now attempt to first connect at 115200 baud
    and then fallback to 9600 baud if that fails. This allows the library
    to work with both new and older MiP robots...it just takes a bit longer
    to connect with the newer MiP robots while it tries 115200 baud first.
    [mip.cpp, mip.h]
2018-09-22 Interleave 115200 and 9600 baud init attempts
    Fixes issue #14.
    Fix is based on @Tiogaplanet 's feedback to my previous commit.
    [mip.cpp, mip.h]
2018-10-09 Add unverified LED update APIs
    Implements feature request #15. These new APIs allow the chest LED and
    head LEDs to be set without the overhead of verifying that the MiP
    successfully received and applied the LED state change. Can be useful
    if the developer will be setting the LED state multiple times per
    second anyway so that a missed state change wouldn't be noticed by a
    user.
    [ChestLED.ino, HeadLEDs.ino, mip.cpp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]

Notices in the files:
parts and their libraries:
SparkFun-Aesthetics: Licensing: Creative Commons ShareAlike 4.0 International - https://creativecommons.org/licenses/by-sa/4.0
